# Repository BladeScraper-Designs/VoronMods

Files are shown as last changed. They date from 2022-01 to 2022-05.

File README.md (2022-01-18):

# VoronMods
My own mods for Voron printers.  Some of them are in VoronUsers already, some are here because they have not yet been submitted to be added (or are waiting to be approved)

Current list of mods:

## Voron 2.4
[Microswitch_Pod_With_Conector](/V2.4/Microswitch_Pod_With_Conector)<br>
[Horizontal-Spool-Holder](/V2.4/Horizontal-Spool-Holder)<br>

## Voron 0.1
[CornerPanel_SpoolHolder](V0.1//CornerPanel_SpoolHolder)<br>
[V0.1_OLED_Expander](/V0.1/V0.1_OLED_Expander)<br>

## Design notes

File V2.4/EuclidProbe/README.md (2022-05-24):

# Voron2 Euclid
Info on setting up the Euclid is pretty scarce, especially for the Voron 2.4.  I put this together to hopefully help people get theirs setup.  

# Note! It has been brought to my attention that a lot of the files on the EuclidProbe GitHub have been updated, including a new gantry mount design and new config.  I am currently in the process of testing these out and am updating the readme as I am able.

## STLs

### Dock

I am not personally a fan of the bed rail mounted dock for Euclid, so I opted to not use it.  If you decide you want to use it, you will need to make changes to the config to make it work.  Why don't I like the bed rail mount?  Well, it just doesn't work very well with a printer that has a flying, tilting gantry.  The first QGL is nearly impossible to get working in my experience, due to the fact that the printer doesn't know the toolhead's true Z position until it is QGLd, and it's hard to pick up the probe to run QGL when the printer doesn't know where the toolhead (and thus, probe mount) actually is.  Some people have gotten it working, but in my opinion for ease of build and setup, as well as deploy reliability, the gantry mount is a much better option.

For the gantry mount, you'll need these two STLs.
https://github.com/nionio6915/Euclid_Probe/blob/main/stls/Voron/VoronGantryMountRev_4Dock.stl
https://github.com/nionio6915/Euclid_Probe/blob/main/stls/Voron/VoronGantryMountRev_4.stl

Accompanying hardware: <br>
Attaching Dock Mount to Gantry: <br>
1 x M5x16 <br>
1 x M5x30 <br>
Attaching the dock itself to the dock mount: <br>
1 x M5x16 <br>
1 x M5 Nut <br>

You may have to fiddle with your motor wires a bit.

### Probe Mount (Toolhead) 
You've got a couple of options here.  

1. You can use the custom carriage with the mounting for the probe built in.  This is super nice, but will involve disassembling your carriage, which is kind of a pain.  Much easier on a new build using Euclid.  Note that as of now this only works with CW1.

You'll need these STLs.  Both now use M2.5 self tapping screws, instead of M3 with heatserts.

MGN9x2 (Voron 2.4 Original Design)
https://github.com/nionio6915/Euclid_Probe/blob/main/stls/Voron/Clockwork1_2XMGN9_Native_RightM2.5.stl
https://github.com/nionio6915/Euclid_Probe/blob/main/stls/Voron/Clockwork1_2XMGN9_Native_LeftM2.5.stl

MGN12 (Voron 2.4R2 and Trident)
https://github.com/nionio6915/Euclid_Probe/blob/main/stls/Voron/Clockwork1_MGN12_Right_M2.5.stl
https://github.com/nionio6915/Euclid_Probe/blob/main/stls/Voron/Clockwork1_MGN12_Left.stl

2. You can simply use the Omron adapter.  For the dock chosen above, you need this STL.  This also uses M2.5 self tappers.  There's not a lot to do here, just make sure when the probe is not attached that the mount itself is above the nozzle to avoid crashes.
https://github.com/nionio6915/Euclid_Probe/blob/main/stls/Voron/OmronFotekM2_V3.stl

## Config
# I will soon be updating this as needed using methods from the new Euclid config.  For now, though, the below instructions still work.

I started off with the default Euclid Klipper config, but I found it suboptimal and somewhat hard to understand.  I customized it, and added comments to make it easier for you to understand what you'll need to change.  I also wanted to implement auto Z, so I did.

This is my Euclid probe cfg.  You can either download it and add [include euclid.cfg] to your printer.cfg, or copy its contents and paste them directly into your own config.  I created a subdirectory in my .cfg folder called Euclid to make it a bit more organized.  If you do so, it'll be [include Euclid/euclid.cfg].  
https://github.com/BladeScraper-Designs/VoronMods/blob/main/V2.4/EuclidProbe/cfg/euclid.cfg

And this is my config for Auto Z.  If you don't want to use auto Z calibration, simply ignore this file and remove [include auto_z.cfg] from euclid.cfg. <br>
https://github.com/BladeScraper-Designs/VoronMods/blob/main/V2.4/EuclidProbe/cfg/auto_z.cfg

These configs aren't quite as easy to modify as the official Auto_Z and Euclid/Klicky configs, but they should be a decent starting point.  You may need to refer to those official configs to ensure you know what you are changing.  I tried to add notes where I can, but really can't come close to their level of detail in some places.

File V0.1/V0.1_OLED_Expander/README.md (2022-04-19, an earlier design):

## Purpose

The purpose of this mod is to provide an additional MCU to the V0.1 to drive a small OLED display in the skirt, as well as provide a rotary encoder interface for the menus.  Originally, the reason I started on the design was because I was running into I2C timeout errors on my SSD1306 display when running it directly off of the SKR mainboard in my V0.1, due to the extremely long wire runs which I2C was not designed for.  After all - I2C stands for Inter-Integrated Circuit, and was designed to connect two ICs locally on a single PCB.  As such, it does not do well with long wire runs such as the one I was using to drive the display originally.  

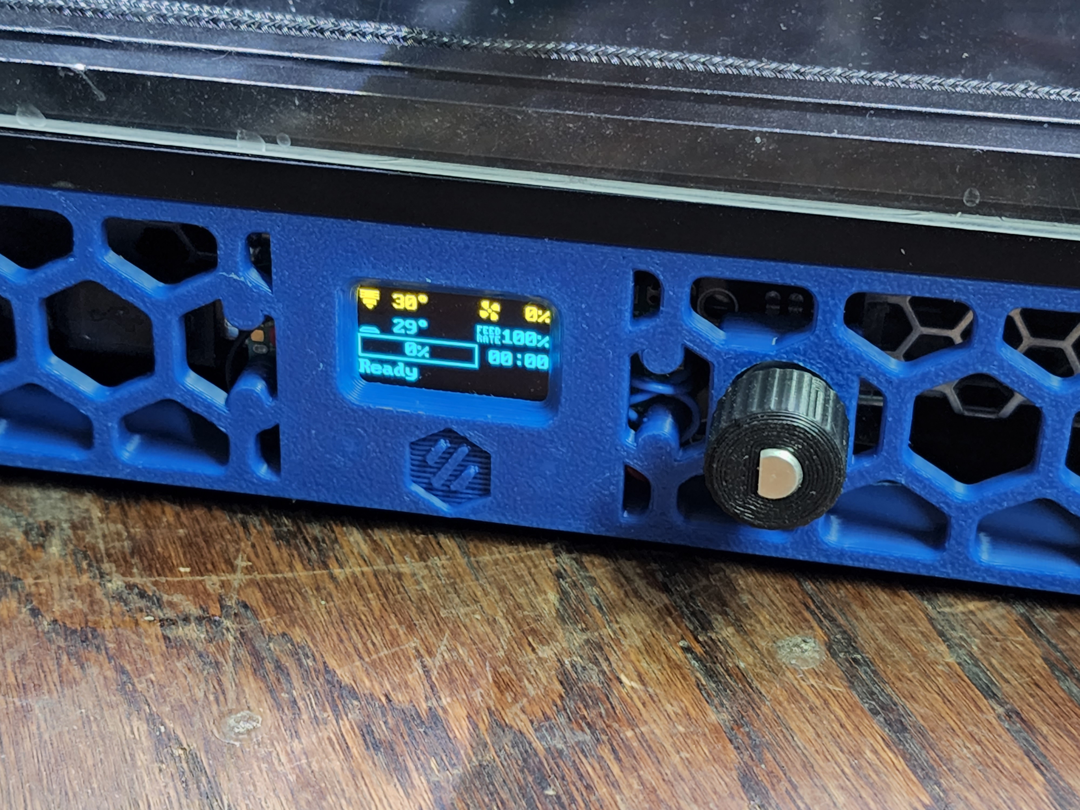
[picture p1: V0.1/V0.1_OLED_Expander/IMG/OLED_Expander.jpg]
<br>

It utilizes a Raspberry Pi Pico MCU, which became supported in Klipper not too long ago.  At only $4 a piece, it offers an extremely affordable way to add an MCU to your V0.1.  The display itself is a SSD1306 0.96" I2C-Controlled OLED from UCTRONICS on Amazon, though I'd wager just about any 0.96" I2C OLED panel you buy will work as they all seem to have the same layout and dimensions.  The encoder is a typical KY-040 encoder, available for very cheap all over the place. The Pico then connects to the Raspberry Pi running Klipper over USB, and that's it!

Becuase this is an entirely separate MCU, you can do a lot more with it than just driving a small display and the encoder.  You could easily add some wiring to connect to an ADXL345 to run input shaper (custom wiring harness and connector required), drive some NeoPixels, control an external MOSFET for e.g. fan control, and more.  

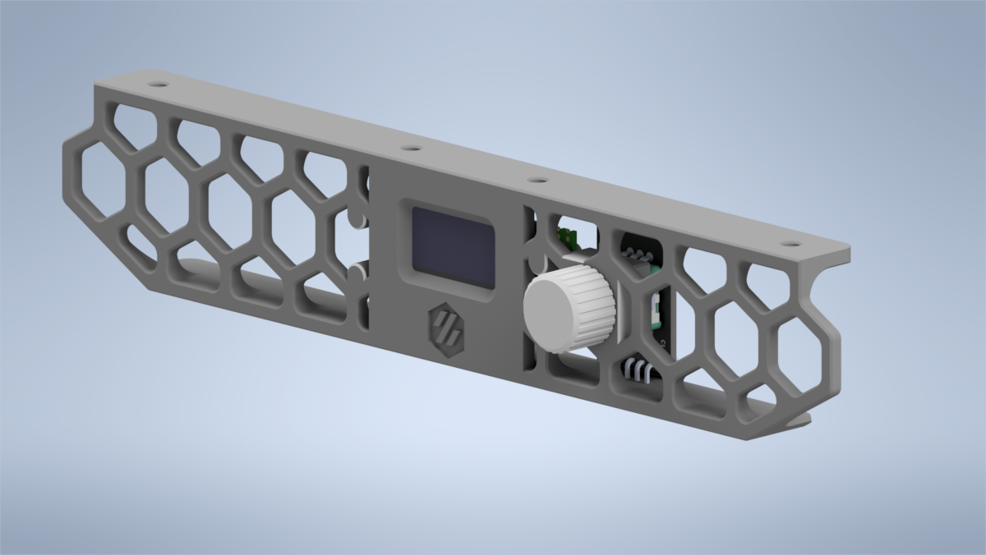
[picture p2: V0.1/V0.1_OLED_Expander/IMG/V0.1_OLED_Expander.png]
<br>

## Wiring the display to the Pico MCU

Seeing as the display uses I2C wiring is super simple, using only four wires of which two are used for power. <br>
** IMPORTANT ** the Pico GPIO is only rated to 3.3V.  I'm not sure if the SSD1306 modules have internal level shifters to ensure the I2C level is kept at 3.3V when powered by 5V, so I'd power the display from 3.3V rather than 5V just to be safe.
Wire them together according to the below list.  I prefer to desolder the pins from the OLED display and solder directly to the pads to keep it as low profile as possible.  

VCC --> 3V3 <br>
GND --> GND <br>
SCK --> GP1 <br>
SDA --> GP0 <br>

## Wiring the encoder to the Pico MCU

The encoder wiring is also quite simple.  Follow the below list.  You will need to either cut off/desolder the pins or bend them out of the way, because how they come out of the package the pins will hit the skirt piece.

VCC --> 3V3 <br>
GND --> GND <br>
SW --> GP18 <br>
DT --> GP17 <br>
CLK --> GP16 <br>

## Making the Pico Firmware

To flash the Pico MCU, SSH into your Pi and enter these commands.

1. cd ~/klipper
2. make clean
3. make menuconfig <br>
    Micro-controller Architecture should be set to "Raspberry Pi RP2040" <br>
    Communication Interface should be USB <br>
4. Q (asks you to save, hit Y)
5. make

## Flashing your Pico

Once the make commmand is finished, there's a couple ways to flash the firmware to the Pico.  You can either do it on the Pi itself (faster), or use FTP to grab the firmware from the Pi and use a Windows PC to copy it to the Pico (easier).  These instructions are the easier way:

1. Use FileZilla or a similar FTP program to log into the Pi and download klipper.uf2 from ~/klipper/out
2. Put your Pico into bootloader mode.  To do this, plug the Pico into your PC while holding the BOOTSEL button.  It will pop up on This PC as a mass storage device with a capacity of 128MB.
3. Copy the klipper.uf2 to the Pico.  Once copied, it will automatically unmount from the PC, reboot, flash, and that's it. 

## Setting up .cfg 

Once done with flashing the Pico, all you have to do is upload the pico.cfg I've included to the config folder on your main Pi, then add [include pico.cfg] to your main printer.cfg.  Alternatively, you can just copy the contents of pico.cfg to your main printer.cfg.  I prefer the separate cfg myself, though.

Plug the Pico into your Pi via USB, run the cable as needed, then do the same commands you normally do to find the serial ID of the new MCU:

1. ls -l /dev/serial/by-id <br>
    it will be something like /usb-Klipper_rp2040.  
2. copy that serial ID and replace what's currently in pico.cfg.

Once that's done, you should be able to do a firmware restart and see your new OLED display working just as intended.  You can also test your encoder to ensure it is working.  Note that for some reason the click part of the encoder seems to lag a bit, I'm not really sure why.  The scrolling, however, is very responsive.

STEP files have also been included in /CAD to allow you to add whatever you want to the skirt.  

## Notes
1. An 18" micro USB seems to be the perfect length. Obviously longer will work, but you'll need to wrap it around itself a few times to shorten it.  The [MonoPrice 1.5ft Micro USB](https://smile.amazon.com/gp/product/B002HZYBZ6) cable on Amazon is exactly what I am using, and it works great.
2. If you plan to drive NeoPixels with this, beware that it's powered only by the 5V USB line, so you'll be limited in the number of NeoPixels you can drive off the Pico directly.
3. You only need to use the two outermost holes in the skirt to screw the Skirt down.  It has four since it was made using the two separate skirt pieces, but in reality one on each end is fine.  It'd be pretty hard to access the ones towards the middle anyway, what with the Pi and stuff in the way.
4. The hole in the skirt for the encoder is closed off for printability.  It's only one or two layers thick, so that you're not trying to bridge in a circle.  This allows printing without supports.  Once printed, simply use an X-Acto knife or similar to cut out the thin layers.
5. In order to use the Knob_Shortened.stl provided in STLs/CAD, you need to shorten the encoder spline by 5mm.  I found the knob it comes with to be disproportionately long.  Alternatively, I've included the STLs and CAD for the same knob but with a hole in the end (Knob_Through.stl) to allow the spline to extend past.  It looks a bit silly, but it works if you don't have the equipment to shorten the spline on the encoder.
6. You may have to trim a little bit of the PCB on the encoder at the bottom to prevent it from rubbing on/hitting the skirt.  
7. For some reason, when you first start up the printer, or restart Klipper, the display acts like you clicked the encoder button, and enters the menu.  I am not sure why this is.  If you have any suggestions, or manage to figure out why and/or fix it, I'd love to hear from you.
8. The encoder sticks out quite a bit in the back, inside the skirt.  You may need to move your PSU just slightly inward to avoid the encoder body interfering with the PSU.
9. One weird thing about these SSD1306 OLED displays is that they often have a different color for the top row.  I'm not really sure why this is, but naturally that means the top row of the mdnu will always be that color (in my case, yellow).  I believe there are some of these that are all one color, but that's not what I have.

## USB Cable Routing
This is the best routing I've found for the USB cable. 

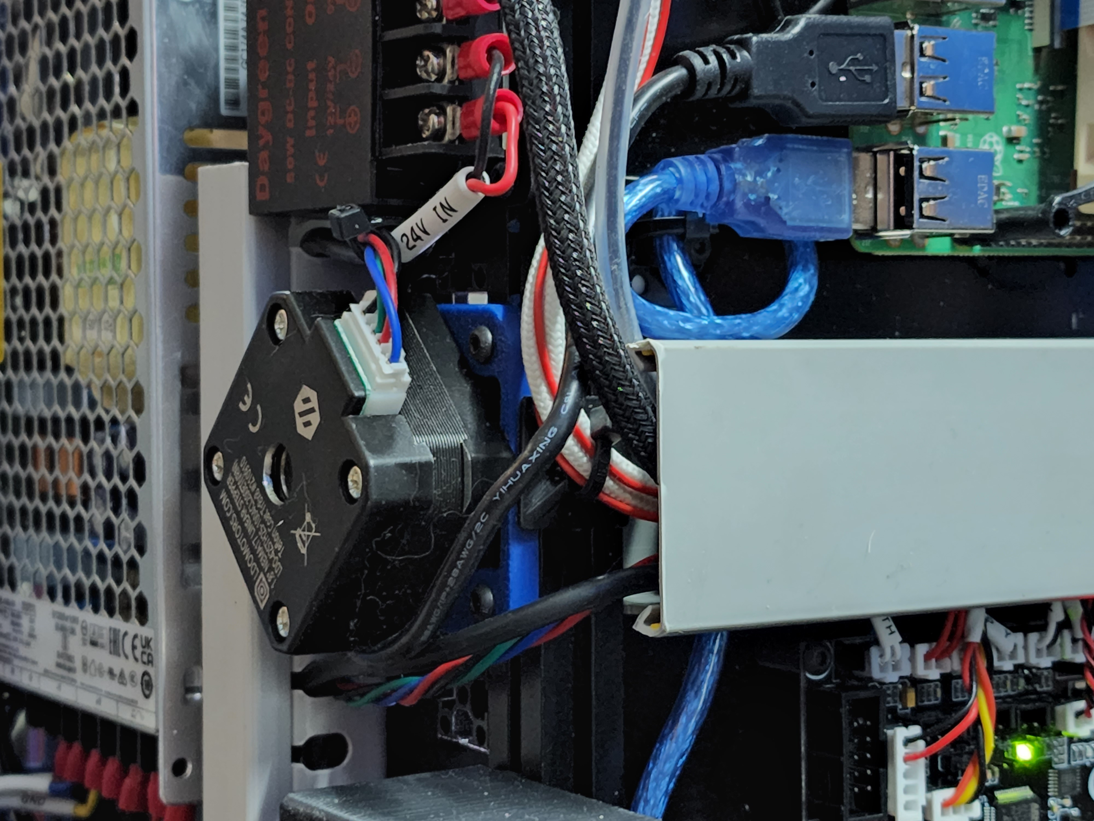
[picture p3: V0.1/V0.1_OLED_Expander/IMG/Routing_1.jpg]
<br>
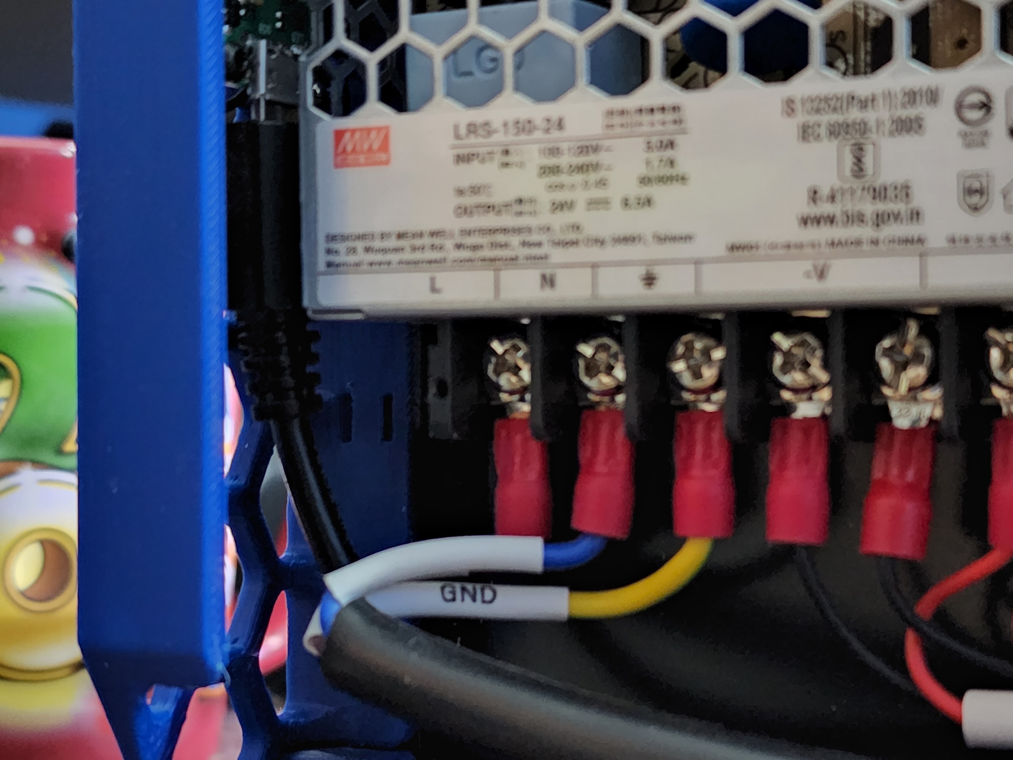
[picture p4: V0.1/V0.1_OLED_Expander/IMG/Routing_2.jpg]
<br>

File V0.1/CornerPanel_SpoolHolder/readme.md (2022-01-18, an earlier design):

## Purpose
I originally came up with this mod in order to accommodate my custom hinged rear panel.  The stock spoolholder gets in the way of the hinging panel and won't allow it to open without removing the spool holder.  This mod moves the spoolholder to the top rear corner panel clip, allowing for easier access to the rear panel as well as providing a more secure mount.  It requires minimal hardware and is very easy to install.

## Required Hardware
1 x M3 Nut (Square, Hex, or NoDropNut, any will work) <br>
2 x M3x10 BHCS

## Print Settings
4 Walls, 5 Top/Bottom, 40% Infill <br>
Standard Voron structural part settings.  You do want this to be relatively strong.

## Install Instructions
1. Remove stock spool holder.  You can reuse the PTFE lengths.
2. Remove left side panel.  
3. Remove top rear corner panel clip from the acrylic panel.  Hopefully you used VHB instead of glue :)
4. Install the modified CornerPanel onto the side panel.  
5. Remove rear left foot and install one extra M3 dropnut (or use NoDropNuts Mod) onto the left side of the rear left extrusion.
6. Reinstall side panel.
7. Install the spool holder using the M3x10 BHCS.   One of them will replace the original M3x8 in the old panel clip.

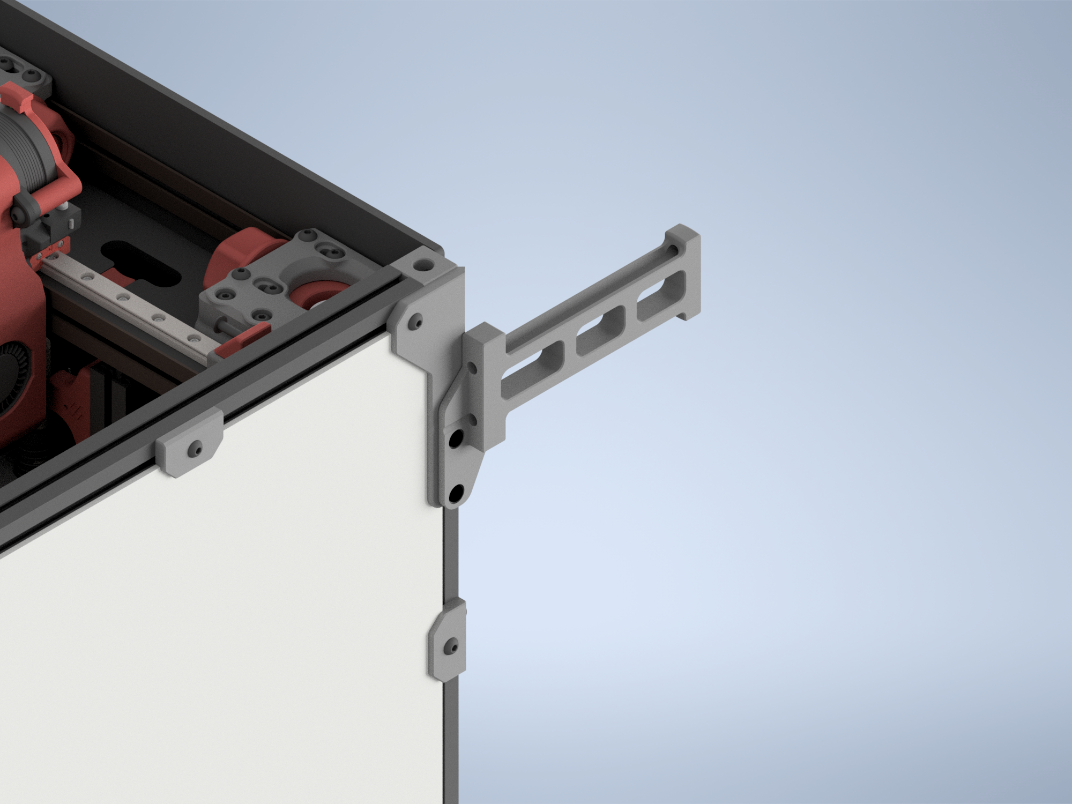
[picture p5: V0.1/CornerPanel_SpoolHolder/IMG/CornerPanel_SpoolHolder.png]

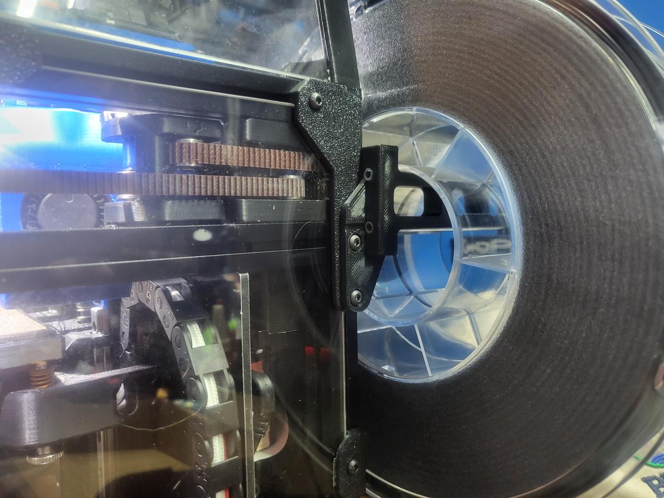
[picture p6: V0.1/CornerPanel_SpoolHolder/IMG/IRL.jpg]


## Notes
There are four different CornerPanel files.  Each one is sized to different panel thicknesses, like the originals.  Pick one that matches your panel thicknesses.  There is an additional 3.25mm size just because a lot of 3mm panels tend to be actually 3.15-3.25mm in my experience.  

If you find that your spoolholder is slightly skewed to one side or the other, the CAD files are supplied so you can extrude them slightly thicker or thinner to get the spoolholder to stick out perfectly straight.  If this part is too thick for your panels, the spoolholder will be skewed slightly to the left (when viewed from the back of the printer).  If it's too thin for your panels, it'll be skewed to the right.

When properly sized, the spoolholder will be perfectly straight out the back, and there's little to no chance for the edge of the spool to rub on your back panel.
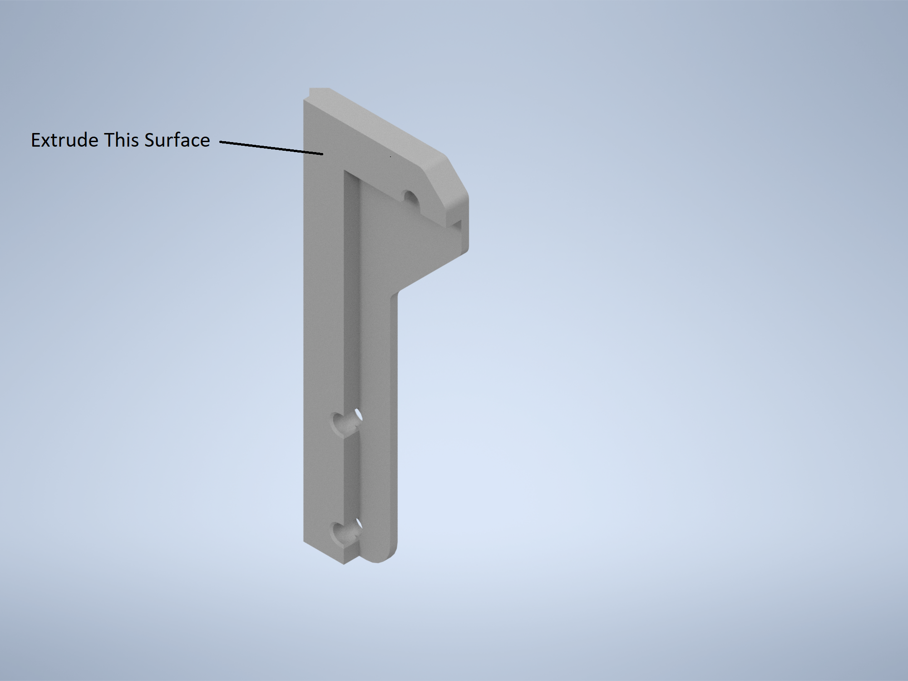
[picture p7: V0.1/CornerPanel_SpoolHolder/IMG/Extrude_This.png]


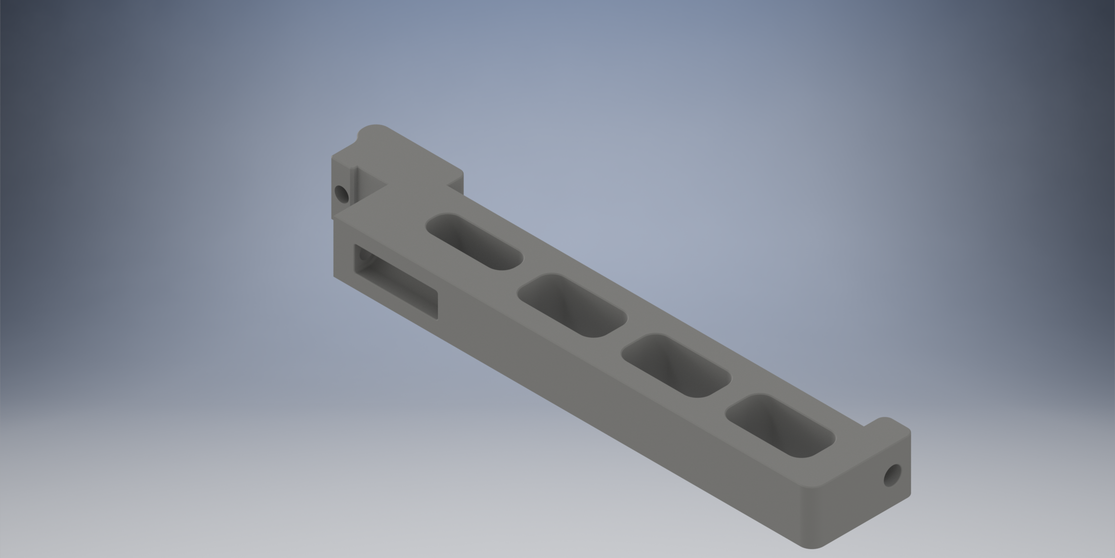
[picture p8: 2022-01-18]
V2.4/Horizontal-Spool-Holder/img/Holder_1.png

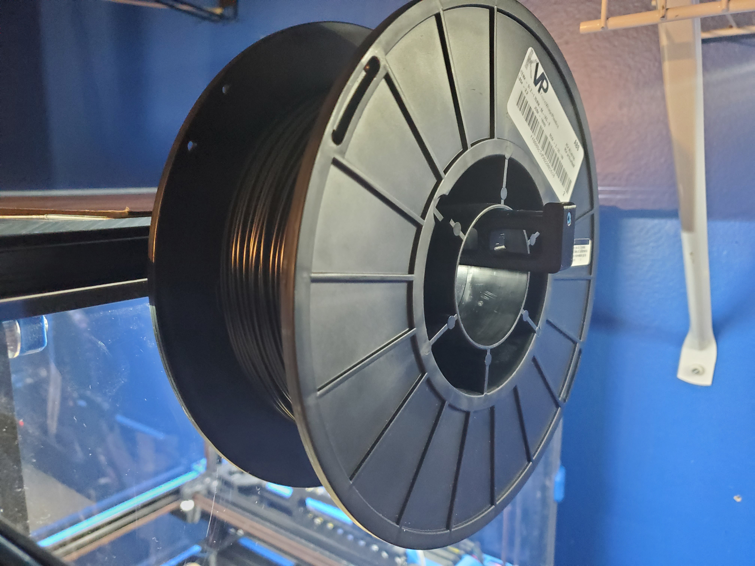
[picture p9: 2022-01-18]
V2.4/Horizontal-Spool-Holder/img/Holder-with-spool.jpg

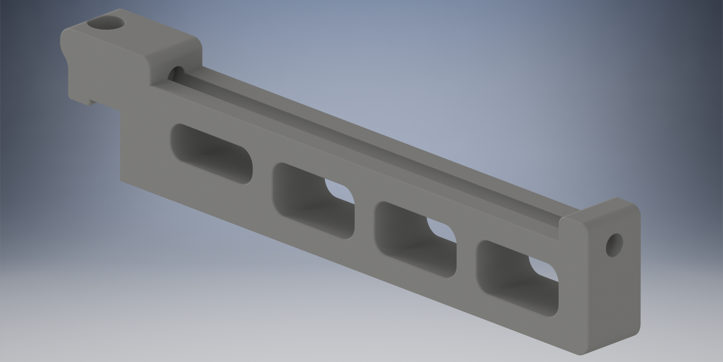
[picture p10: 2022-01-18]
V2.4/Horizontal-Spool-Holder/img/Holder.png

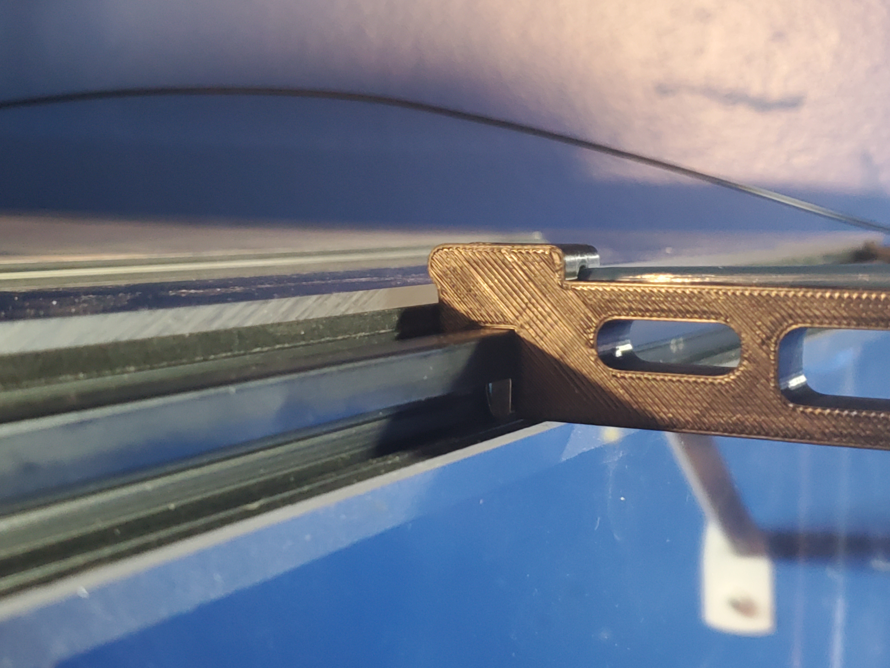
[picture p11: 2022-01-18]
V2.4/Horizontal-Spool-Holder/img/Holder-Real.jpg

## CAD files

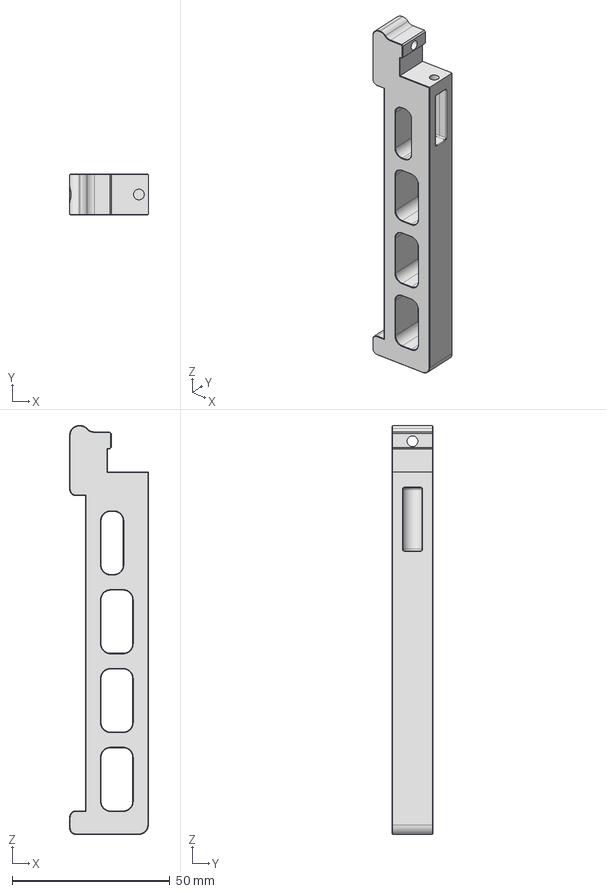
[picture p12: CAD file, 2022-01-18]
V2.4/Horizontal-Spool-Holder/Holder.stp
25.0 x 13.0 x 129.8 mm

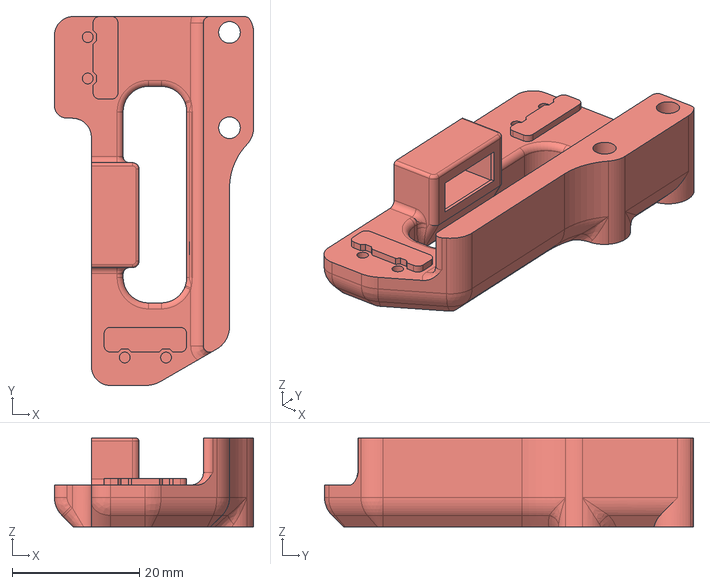
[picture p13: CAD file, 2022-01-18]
V2.4/Microswitch_Pod_With_Conector/Microswitch_Pod_Connector.stp
31.4 x 58.0 x 14.0 mm

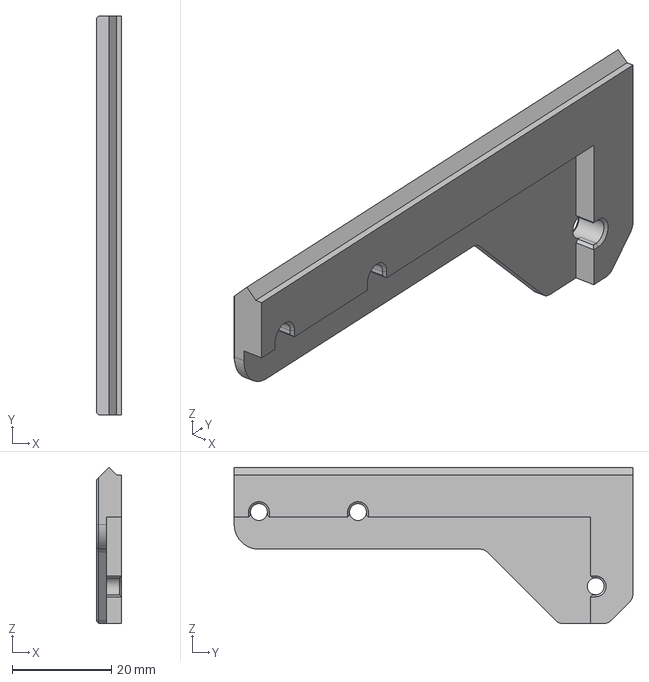
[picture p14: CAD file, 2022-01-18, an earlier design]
V0.1/CornerPanel_SpoolHolder/CAD/CornerPanel/CornerPanel_3mm.stp
5.00 x 80.5 x 31.5 mm

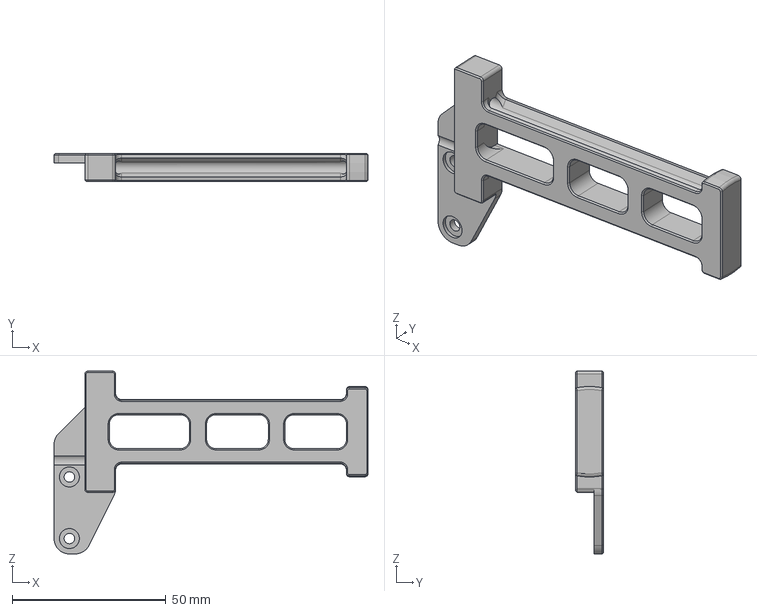
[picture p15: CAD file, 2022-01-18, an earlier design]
V0.1/CornerPanel_SpoolHolder/CAD/SpoolHolder.stp
102.0 x 9.00 x 59.4 mm

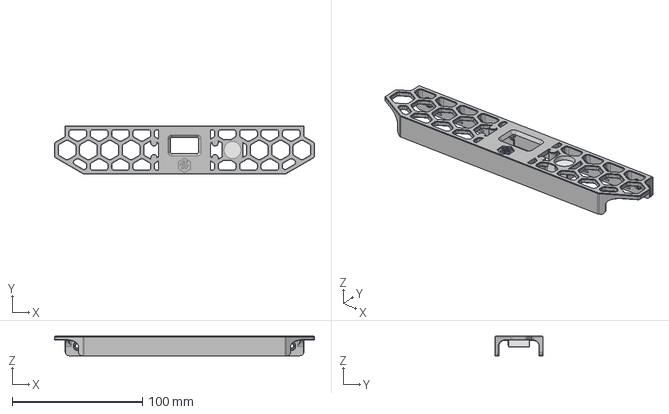
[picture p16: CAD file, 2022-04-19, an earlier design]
V0.1/V0.1_OLED_Expander/CAD/Skirt_OLED_With_Encoder.stp
200.0 x 37.0 x 15.0 mm

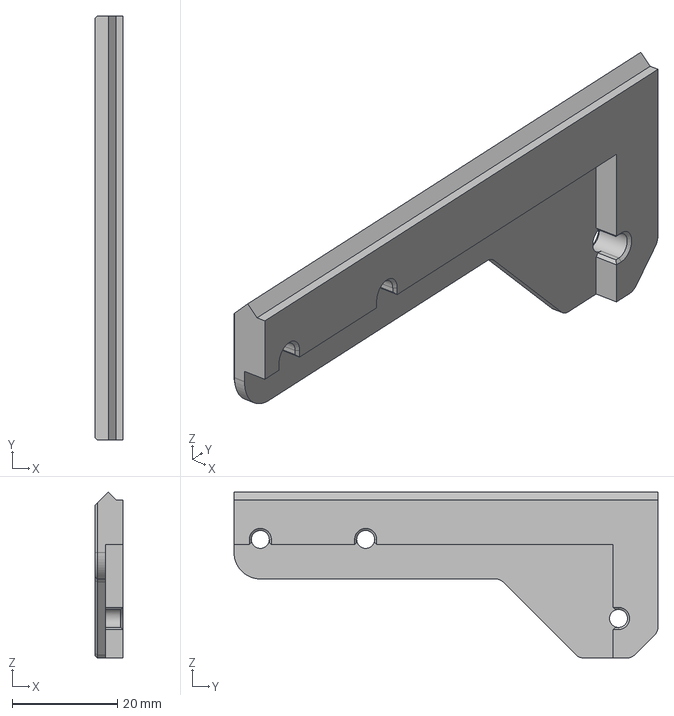
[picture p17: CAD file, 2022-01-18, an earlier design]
V0.1/CornerPanel_SpoolHolder/CAD/CornerPanel/CornerPanel_3.25mm.stp
5.25 x 80.5 x 31.5 mm

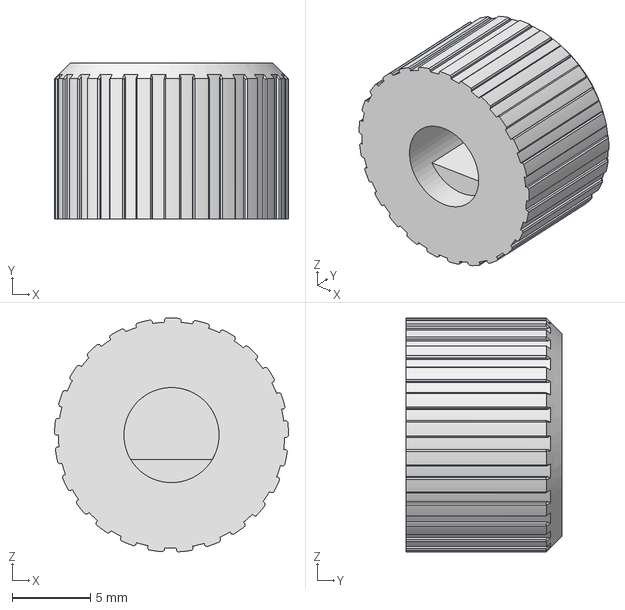
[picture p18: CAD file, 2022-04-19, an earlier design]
V0.1/V0.1_OLED_Expander/CAD/Knob_Shortened.stp
15.0 x 10.0 x 15.0 mm

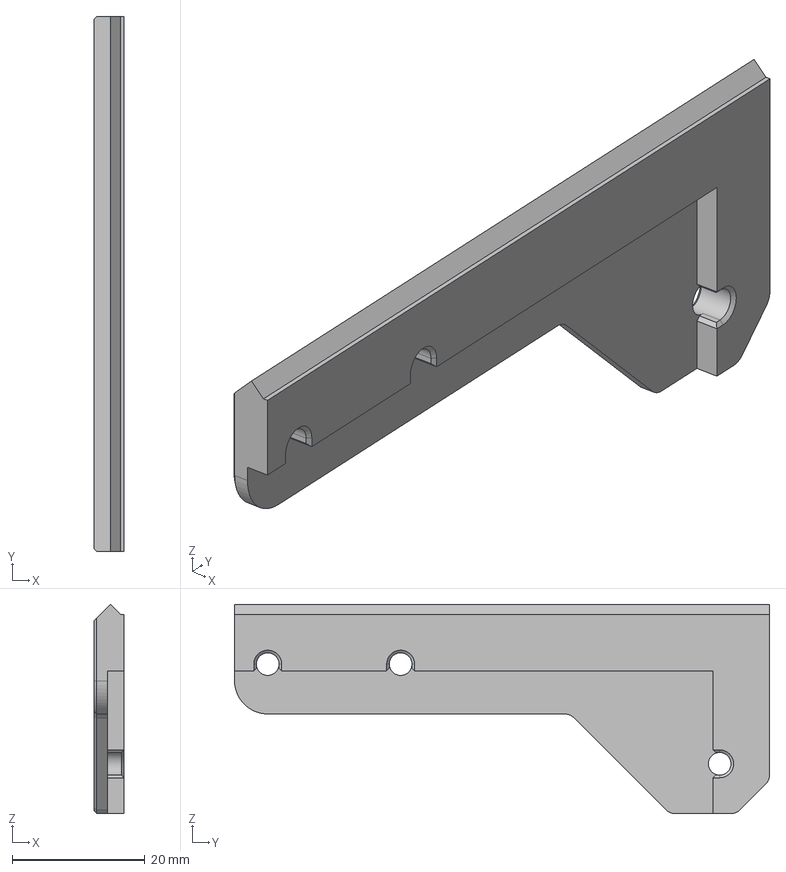
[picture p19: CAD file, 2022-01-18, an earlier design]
V0.1/CornerPanel_SpoolHolder/CAD/CornerPanel/CornerPanel_2.5mm.stp
4.50 x 80.5 x 31.5 mm

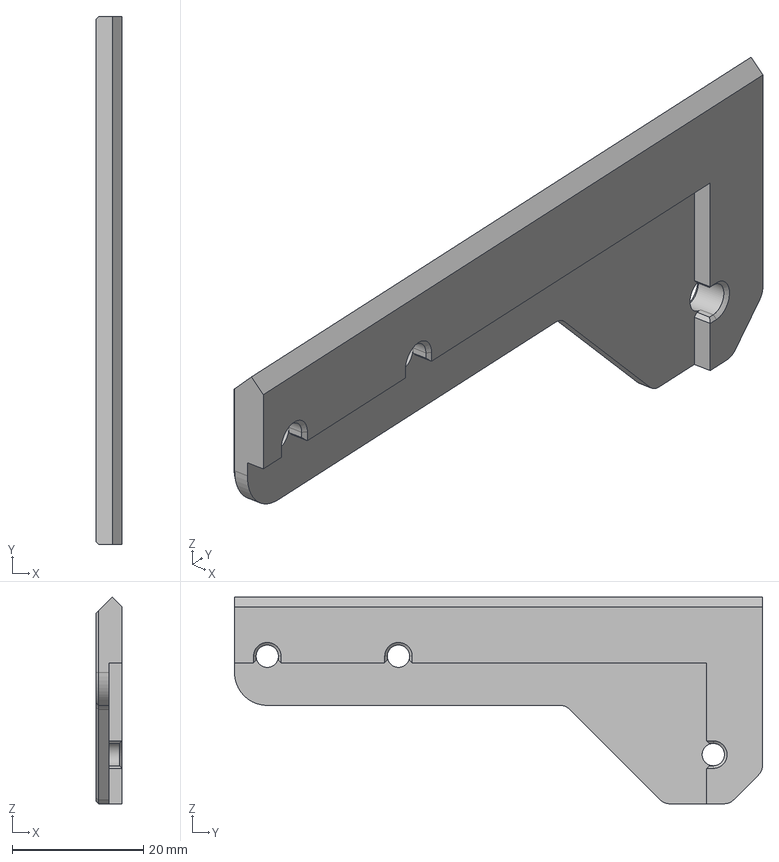
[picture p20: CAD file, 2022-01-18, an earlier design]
V0.1/CornerPanel_SpoolHolder/CAD/CornerPanel/CornerPanel_2mm.stp
4.00 x 80.5 x 31.5 mm

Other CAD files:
V0.1/V0.1_OLED_Expander/CAD/Knob_Through.stp
V0.1/CornerPanel_SpoolHolder/STL/CornerPanel/CornerPanel_2.5mm.stl
V0.1/CornerPanel_SpoolHolder/STL/CornerPanel/CornerPanel_2mm.stl
V0.1/CornerPanel_SpoolHolder/STL/CornerPanel/CornerPanel_3.25mm.stl
V0.1/CornerPanel_SpoolHolder/STL/CornerPanel/CornerPanel_3mm.stl
V0.1/CornerPanel_SpoolHolder/STL/SpoolHolder.stl
V0.1/V0.1_OLED_Expander/STL/Knob_Shortened.stl
V0.1/V0.1_OLED_Expander/STL/Knob_Through.stl
V0.1/V0.1_OLED_Expander/STL/Skirt_OLED_With_Encoder.stl
V2.4/Horizontal-Spool-Holder/Holder.ipt
V2.4/Horizontal-Spool-Holder/Holder.stl
V2.4/Microswitch_Pod_With_Conector/Microswitch_Pod_Connector.stl

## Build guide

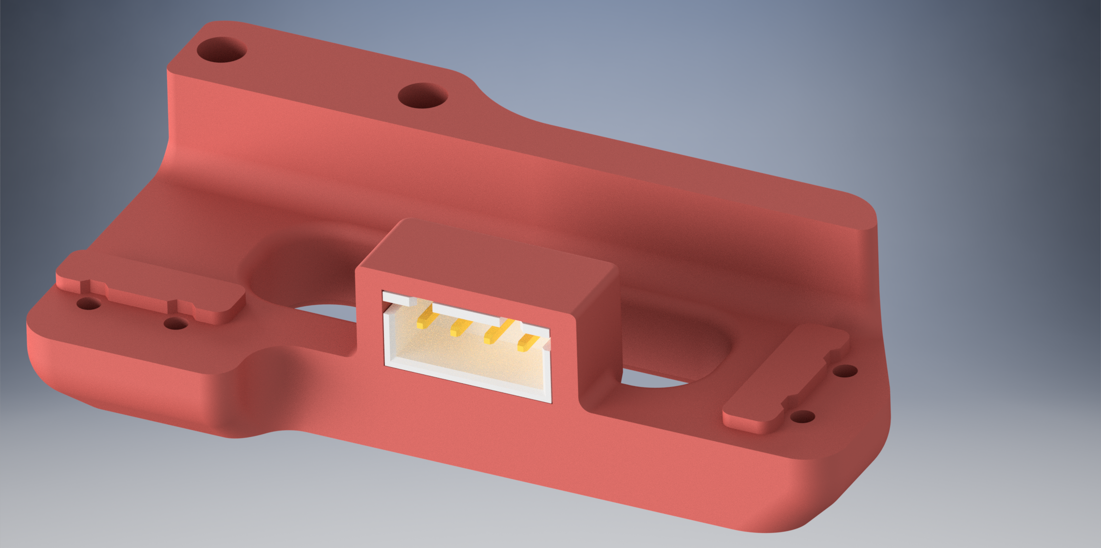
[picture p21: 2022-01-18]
V2.4/Microswitch_Pod_With_Conector/img/assembly.png

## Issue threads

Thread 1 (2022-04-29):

Euclid Updates

nionio6915, 2022-04-29:
Blade Scraper-

Thanks for posting these! A few comments / updates you might want to include:

1. The 2 piece Gantry mount has been revised to use 1- M5x16 and a 1-M5x30, matching the BOM.
2. The dock also uses 1-M5x16 screw and nut to attach to the gantry.
3. klipper config and macros have been updated:
   -v3 is hard coded positions
   -v4 tries to use array variables so you enter them once.
4. Probe Mount- the most current one is a tad shorter and has holes for M2.5 self tapping plastic screws. We've found the heatsert one can be a little fussy.

The 2-piece dock is recommended becasue adjusting the dock/probe height is easy via the thru-hole in the dock instead of fussing with the Omron mount.

We appriate your contributions and will likely add some in for other to follow.

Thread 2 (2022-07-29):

V0 OLED skirt

kymlalu, 2022-07-29:
Since i don't know how to contact you i try this.
For that rotary encoder which acts as pushed after startup/restart, just add ! before pin. So in my config i have this "click_pin: ^!pico:gpio13" . I'm using internall pull-up so i have here "^" in addition to " ! ",

BladeScraper-Designs, 2022-11-27:
Hey man thanks.  Sorry it's been like... Forever since you sent this lol.  But yes that worked.  I had actually tried this before, but I put them in the wrong order (I was doing pico:^!gpio18 instead of ^!pico:gpio18).

Cheers!

Keith
________________________________
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

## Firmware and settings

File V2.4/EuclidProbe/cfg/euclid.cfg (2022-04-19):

[include auto_z.cfg]

###################################################################################################
## HOMING OVERRIDE
###################################################################################################
[force_move]
enable_force_move: True  ; this is necessary to allow SET_KINEMATIC_POSITION to work, so that we can raise Z by 15 even when the printer doesn't know its current kinematic position.

[homing_override]   ## forces Z to raise despite not having been homed, to prevent a nozzle crash if the gantry is physically lower than something that it can hit
gcode:
  SET_KINEMATIC_POSITION Z=0
  QUERY_PROBE
  G0 Z25 F3600           ; raise bed to 15
  G28 X Y                ; home X & Y
  M402
  G0 X122 Y355 F24000    ; CHANGE THE XY COORDINATE TO YOUR SAFE Z HOMING POSITION.  Depends on where your Z endstop is.
  G28 Z                  ; home Z
  G0 Z15 F3600           ; raise bed to 15

###################################################################################################
## ERROR HANDLING
###################################################################################################

[gcode_macro do_error_if_probe_deployed]
gcode:
    {% if not printer.probe.last_query %}
      {action_raise_error("probe already deployed - remove and return to dock")}
    {% endif %}

[gcode_macro error_if_probe_deployed]
gcode:
    G4 P300
    QUERY_PROBE
    do_error_if_probe_deployed

[gcode_macro do_error_if_probe_not_deployed]
gcode:
    {% if printer.probe.last_query %}
      {action_raise_error("probe unsuccessfully deployed")}
    {% endif %}

[gcode_macro error_if_probe_not_deployed]
gcode:
    G4 P300
    QUERY_PROBE
    do_error_if_probe_not_deployed

###################################################################################################
## POSITIONING
###################################################################################################

[gcode_macro move_to_dock]  ; this is the actual dock location.
gcode:
  G90
  G0 X39 Y354 F12000     ; CHANGE THE Y COORDINATE TO MATCH YOUR PRINTER.  The exact coordinates can be found by moving the toolhead manually with the controls, and using M114 to report the current positon.
  M400

[gcode_macro move_outside_dock]  ; this is where the toolhead will go just before entering the dock to pick up or drop off the probe.  
gcode:
  G90
  G0 X100 Y354 F12000    ; CHANGE THE Y COORDINATE TO MATCH YOUR PRINTER.  The exact coordinates can be found by moving the toolhead manually with the controls, and using M114 to report the current positon.
  M400

###################################################################################################
## DEPLOY/STOW PROBE
###################################################################################################

# Macro to Deploy Bed Probe
[gcode_macro M401]
gcode:
    G90
    {% if printer.probe.last_query %}
      move_to_dock
      Move_outside_dock
      error_if_probe_not_deployed
    {% endif %}

# Macro to Stow Bed Leveling Probe
[gcode_macro M402]
gcode:
    G90
    {% if not printer.probe.last_query %}
     move_outside_dock           ; move toolhead to dock exit (DOCKEXIT)
     move_to_dock
     M400
     G0 Y335 F6000               ; You want the Y coordinate to be roughly 20mm away from the dock position.  This way the magnets do not attract and pull the probe back off as the toolhead moves away.
     G0 X150
     error_if_probe_deployed
    {% endif %}

###################################################################################################
## REPLACEMENT MACROS
###################################################################################################

[gcode_macro BED_MESH_CALIBRATE]
rename_existing: _BED_MESH_CALIBRATE
gcode:
  QUERY_PROBE
  M401
  _BED_MESH_CALIBRATE
  M402

[gcode_macro QUAD_GANTRY_LEVEL]
rename_existing: _QUAD_GANTRY_LEVEL
gcode:
  QUERY_PROBE
  M401
  _QUAD_GANTRY_LEVEL
  M402

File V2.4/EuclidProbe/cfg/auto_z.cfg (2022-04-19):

#####################################################################
#    Z Calibration
#####################################################################

# comments are original auto_z_calibration comments from the original author.
## comments are my own comments.

[z_calibration]
#   The X and Y coordinates (in mm) for clicking the nozzle on the
#   Z endstop.  
## This is to be the same as your safe Z home position in your
##   standard printer.cfg. 
probe_nozzle_x: 122
probe_nozzle_y: 355

#   The X and Y coordinates (in mm) for clicking the probe's switch
#   on the Z endstop.  
## X+7, Y-22.5 (relative to your probe_nozzle coordinates) seems to be
## a good number to use.  
probe_switch_x: 122
probe_switch_y: 333

#   The trigger point offset of the used switch.
#   This needs to be fined out manually. For more details go to 
#   https://github.com/protoloft/klipper_z_calibration#switch-offset
#   "So, with a smaller offset value, the nozzle is more away from the 
#   bed! The value cannot be negative."
switch_offset: 0.5

#   The maximum allowed deviation of the calculated offset.
#   If the offset exceeds this value, it will stop!
#   The default is 1.0 mm.
max_deviation: 4

#   The distance in mm to move up before moving to the next
#   position. The default is two times the z_offset from the probe's
#   configuration.
clearance: 7.5

#   The moving speed in X and Y. The default is 50 mm/s.
speed: 200

#   If true, the first probing is done faster by the probing speed.
#   This is to get faster down and the result is not recorded as a
#   probing sample. The default is false.
probing_first_fast: true

#   If true, the first probing is done faster by the probing speed.
#   This is to get faster down and the result is not recorded as a
#   probing sample. The default is false.
start_gcode: SET_GCODE_OFFSET Z=0

#   A list of G-Code commands to execute prior to each calibration command.
#   See docs/Command_Templates.md for G-Code format. This can be used to
#   attach the probe.
before_switch_gcode: M401

#   A list of G-Code commands to execute prior to each probing on the
#   mag-probe. See docs/Command_Templates.md for G-Code format. This can be
#   used to attach the probe after probing on the nozzle and before probing
#   on the mag-probe.
end_gcode: M402

#   A list of G-Code commands to execute after each calibration command.
#   See docs/Command_Templates.md for G-Code format. This can be used to
#   detach the probe afterwards.

[gcode_macro CALIBRATE_Z]
description: Add G90 to CALIBRATE_Z macro to avoid conflict with nozzle scrub macro
rename_existing: _CALIBRATE_Z
gcode:
  G90
  _CALIBRATE_Z

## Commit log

2022-01-18 fist commit
    [CornerPanel_2.5mm.stl, CornerPanel_2.5mm.stp, CornerPanel_2mm.stl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]
2022-01-18 initial commit of Skirt_OLED
    [Skirt_OLED.stl, Skirt_OLED_With_EStop.stl, Skirt_OLED_With_EStop.stp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]
2022-04-19 major update to OLED_EXPANDER
    [Skirt_OLED_With_Encoder.stp]
2022-04-19 add stl and STEP
    [Skirt_OLED.stl, Skirt_OLED_With_EStop.stl, Skirt_OLED_With_EStop.stp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]
2022-04-19 Knobs added
    [Knob_Shortened.stl, Knob_Shortened.stp, Knob_Through.stl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]
2022-04-19 add revised files and photos
    [Skirt_OLED_With_Encoder.stl, Skirt_OLED_With_Encoder.stp]
2022-04-19 update euclid configs
    [auto_z.cfg, euclid.cfg]
